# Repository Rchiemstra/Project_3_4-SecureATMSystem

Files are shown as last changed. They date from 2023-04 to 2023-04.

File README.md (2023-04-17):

# Project_3_4-SecureATMSystem

Dit project betreft het opzetten van een bankomgeving met pinautomaten, geldautomaten en beveiliging. Studenten richten in groepen banken op en verzorgen interbancaire communicatie.

## Beschrijving

Dit project betreft de ontwikkeling van een complete bankomgeving, waarbij studenten in groepen een eigen bank zullen oprichten binnen een land en de complexiteit van samenwerking tussen verschillende groepsbanken zullen simuleren. De architectuur van het systeem zal worden ontworpen met aandacht voor kwaliteitsattributen, waaronder security, betrouwbaarheid en robuustheid.

Het project omvat de ontwikkeling van software- en hardwarecomponenten die betrokken zijn bij het pinnen van geld, inclusief geldautomaten en gelddispensers. Daarnaast zullen de studenten zich bezighouden met de communicatie tussen banken, zodat het voor de eindgebruiker mogelijk wordt om bij een andere groepsbank te pinnen op basis van eigen gegevens (pinpas en saldo).

Elke groep zal een land vertegenwoordigen en een eigen bank oprichten. Het project omvat het ontwerpen en ontwikkelen van software voor het beheer van rekeningen, pinautomaten en geldautomaten, evenals het ontwerpen en implementeren van beveiligingsmaatregelen om de privacy en veiligheid van gebruikersgegevens te waarborgen.

Dit project biedt studenten de kans om in een realistische omgeving te werken aan een complex systeem en belangrijke technische vaardigheden te ontwikkelen, zoals systeemarchitectuur, software- en hardwareontwerp en beveiligingsimplementatie.

### Team

| Naam | LinkedIn |
| --- | --- |
| Ruben Hiemstra | [LinkedIn](https://www.linkedin.com/in/ruben-hiemstra-84b9b6127/) |
| Keanu van der Linden | [LinkedIn](https://github.com/KeanuLin) |
| TBA | [LinkedIn] |
| TBA | [LinkedIn] |
| TBA | [LinkedIn] |

### Bestanden / Files

#### doc
Deze map bevat documentatie over het project. Er is een submap genaamd "Fusion360" die 3D-modellen bevat van verschillende componenten in het project, zoals geldautomaten en pinautomaten. Er is ook een PDF-bestand genaamd "pinautomaat v6 v16.pdf" dat een tekening bevat van een pinautomaat. Verder bevat deze map een submap genaamd "img" met afbeeldingen die worden gebruikt in de documentatie van het project.

#### img 
Deze map bevat afbeeldingen die in het project worden gebruikt. Er zijn drie submappen:

- eurobiljetten: Deze submap bevat afbeeldingen van verschillende eurobiljetten, inclusief "10_euro.jpeg", "20_euro.jpeg" en "50_euro.jpeg".

- geldautomaat_spiraal_unittest: Deze submap bevat afbeeldingen die zijn gebruikt bij het testen van de code voor de geldautomaat.

- UI_Ruben_Hiemstra: Deze submap bevat afbeeldingen van de gebruikersinterface van het bankgedeelte van het project, gemaakt door Ruben Hiemstra. Er zijn 12 PNG-bestanden genaamd "1.PNG" tot en met "12.PNG" die screenshots bevatten van verschillende delen van de UI.
README.md: Dit bestand bevat de beschrijving van het project en de inhoud van deze README.

#### src
Deze map bevat alle broncode voor het project, georganiseerd in verschillende submappen.

- Arduino: Deze map bevat de broncode voor de Arduino-microcontroller die wordt gebruikt in het project. Er zijn verschillende submappen binnen "Arduino" die code bevatten voor specifieke componenten en functies, waaronder tests voor verschillende componenten zoals RFID-kaarten en keypads, code voor het printen van bonnen en code voor de master- en node-nodes.

- UI: Deze map bevat de broncode voor de gebruikersinterface van het bankgedeelte van het project, geschreven in Java. Er is een submap genaamd ".vscode" met instellingen voor de Visual Studio Code-editor. De "bank" submap bevat broncode voor het beheer van rekeningen, pinautomaten en geldautomaten, evenals tests en afbeeldingen. De pom.xml-file is een Maven-bestand dat nodig is om de Java-code in dit project te compileren en uit te voeren.

### Media

## Rubben Hiemstra

#### Ontwerp pinautomaat

<a href="https://youtu.be/MVlD1MDzszY" target="_blank"   rel="noopener"  >
    
</a>

#### Test pinautomaat

<a href="https://youtu.be/q1xSIUnEXdo" target="_blank"   rel="noopener"  >
    
</a>

## Groepsgedeelte

#### Ontwerp geldlade

<a href="https://youtu.be/ZYODidJn9q8" target="_blank"   rel="noopener"  >
    
</a>

#### Ontwerp geldlades

<a href="https://youtu.be/2BWyQDWWHVI" target="_blank"   rel="noopener"  >
    
</a>

#### Pinpas blokkeren voor alle bij alle pinautomaten

<a href="https://youtu.be/CWAH8InKsuk" target="_blank"   rel="noopener"  >
    
</a>

#### Meerdere pinautomaten tegelijk

<a href="https://youtu.be/7Nd1Y9njzbA" target="_blank"   rel="noopener"  >
    
</a>

### unittest

Geldautomaat spiraal - Unit test

Voor ons bankproject moeten we geld kunnen afgeven nadat er is gepind. Daarom moeten we een systeem bedenken dat veilig is en geen geld verliest. We hebben besloten om een spiraal te gebruiken waar het geld uit kan vallen. Om zo'n spiraal te maken, hebben we verschillende methoden uitgeprobeerd: het vervormen van staaldraad, 3D-printen en online zoeken. Hieronder beschrijven we de stappen die we hebben genomen tot aan onze beslissing.

<table >
  <tbody>
    <tr>
      <th>Poging 1</th>
    </tr>
    <tr>
      <td>De grijze/De witte</td>
    </tr>
    <tr>
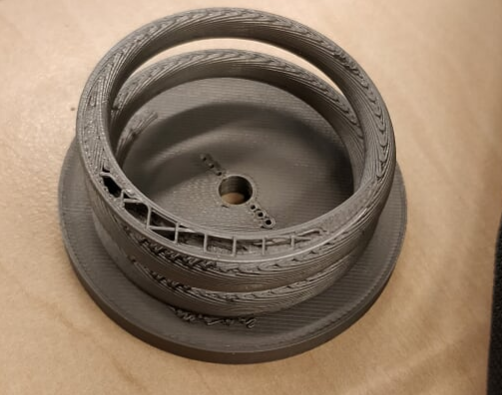
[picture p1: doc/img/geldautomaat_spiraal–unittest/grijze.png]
      <td>
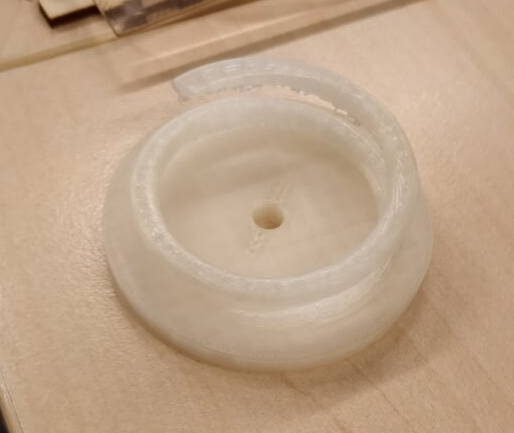
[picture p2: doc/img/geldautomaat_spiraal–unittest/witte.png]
      </td>
    </tr>
    <tr>
      <td>De grijze spiraal is hetzelfde als de witte, maar we hebben ondersteuning gebruikt tijdens het printen. Hierdoor ziet het er beter uit en zijn de cirkels gladder, waardoor het papier niet vast komt te zitten. Helaas hebben we te veel ruimte tussen de cirkels weggehaald, waardoor de ruimte te krap was en de cirkels te zwak waren. Deze poging voldeed daarom niet aan onze eisen.</td>
    </tr>
    <tr>
      <td>Dit is een klein stukje van een 3D-geprinte spiraal. We hebben geen ondersteuning gebruikt tijdens het printen, waardoor er gesmolten plastic aan de onderkant hangt dat het papier kan vasthouden. Bovendien was de ruimte tussen de cirkels waar het papier doorheen moet te groot, waardoor we maar weinig papier konden vasthouden. Om meer papier op te slaan, moeten we de diameter of de dikte van de cirkels verminderen om meer ruimte te creëren.</td>
    </tr>
  </tbody>
</table>

<table>
  <tbody>
    <tr>
      <th>Poging 2</th>
    </tr>
    <tr>
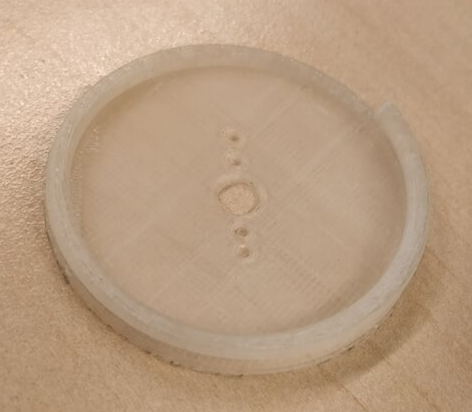
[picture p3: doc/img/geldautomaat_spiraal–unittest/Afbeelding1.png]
      <td>
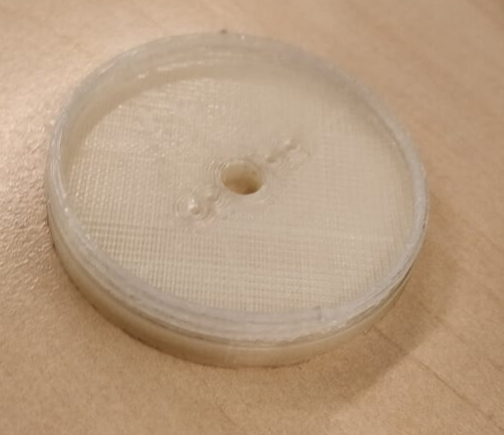
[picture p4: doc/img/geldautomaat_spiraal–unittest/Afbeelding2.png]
      </td>
    </tr>
    <tr>
      <td><p>Bij deze spiraal hebben we meer ruimte voor het papier gemaakt door de afstand tussen de cirkels en de diameter van de cirkels te verminderen. Helaas hebben we te veel afstand weggehaald, waardoor de ruimte te krap was en de cirkels te zwak waren. Deze poging voldeed daarom ook niet aan onze eisen.</p></td>
    </tr>
  </tbody>
</table>

<table>
  <tbody>
    <tr>
      <th>Poging 3</th>
    </tr>
    <tr>
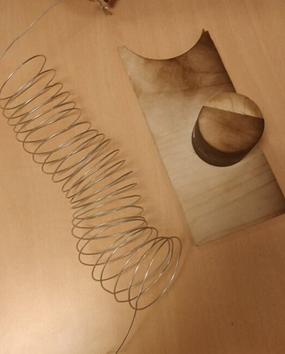
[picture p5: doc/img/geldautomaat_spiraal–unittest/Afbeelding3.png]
      <td></td>
    </tr>
    <tr>
      <td><p>Bij deze poging hebben we geprobeerd staaldraad te gebruiken, omdat dit stevig is en vervormd kan worden. We hebben een stuk hout gebruikt om de draad omheen te draaien en het daarna een tijdje laten zitten om te zorgen dat het goed bleef zitten. Helaas bleek na het verwijderen van de draad dat deze zeer asymmetrisch was en niet bruikbaar was. We zijn daarom teruggegaan naar de 3D-printer.</p></td>
    </tr>
  </tbody>
</table>

<table>
  <tbody>
    <tr>
      <th>Poging 4</th>
    </tr>
    <tr>
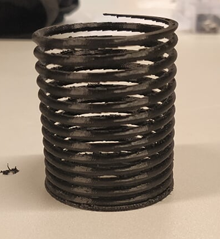
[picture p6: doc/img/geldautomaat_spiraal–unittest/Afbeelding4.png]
      <td> </tr>
    <tr>
      <td><p>Bij deze 3D-print hebben we ondersteuning gebruikt en hebben we de afmetingen op alle mogelijke manieren geoptimaliseerd (dikte, afstand tussen de cirkels en de voet van de print). Dit zou de definitieve versie worden, maar helaas is de 3D-printer uitgevallen en konden we niet verder gaan. We hebben daarom maar de helft van de spiraal kunnen printen. Desondanks zijn we zeer tevreden met het resultaat en zullen we dit gebruiken in onze geldautomaat.</p></td>
    </tr>
  </tbody>
</table>

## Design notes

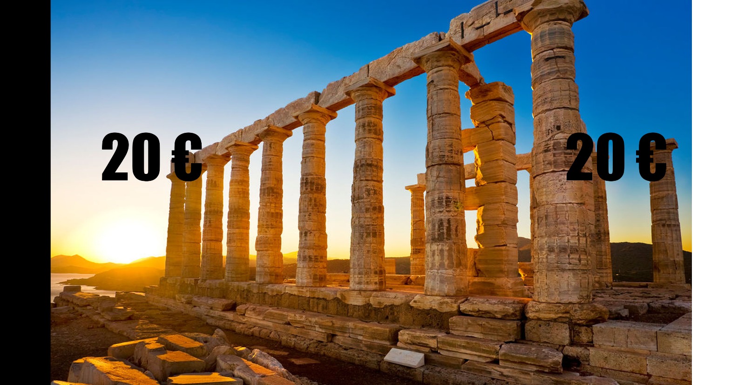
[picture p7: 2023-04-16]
doc/img/eurobiljetten/20_euro.jpeg

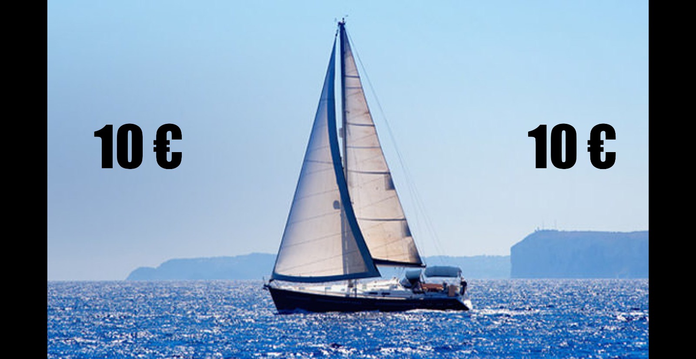
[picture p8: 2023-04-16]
doc/img/eurobiljetten/10_euro.jpeg

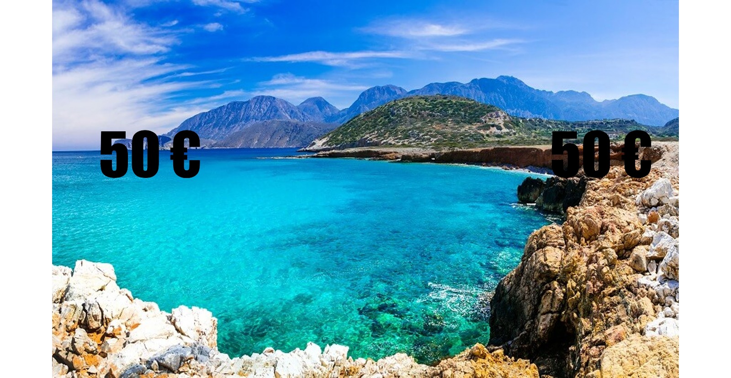
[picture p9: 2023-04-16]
doc/img/eurobiljetten/50_euro.jpeg

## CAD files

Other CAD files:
doc/Fusion360/geldautomaat v12.f3d
doc/Fusion360/geldautomaat v2.f3d
doc/Fusion360/pinautomaat v6 v16.f3d
doc/Fusion360/spiraal v25.f3d

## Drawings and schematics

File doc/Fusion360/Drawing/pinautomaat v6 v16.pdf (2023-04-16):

16.01 6

16

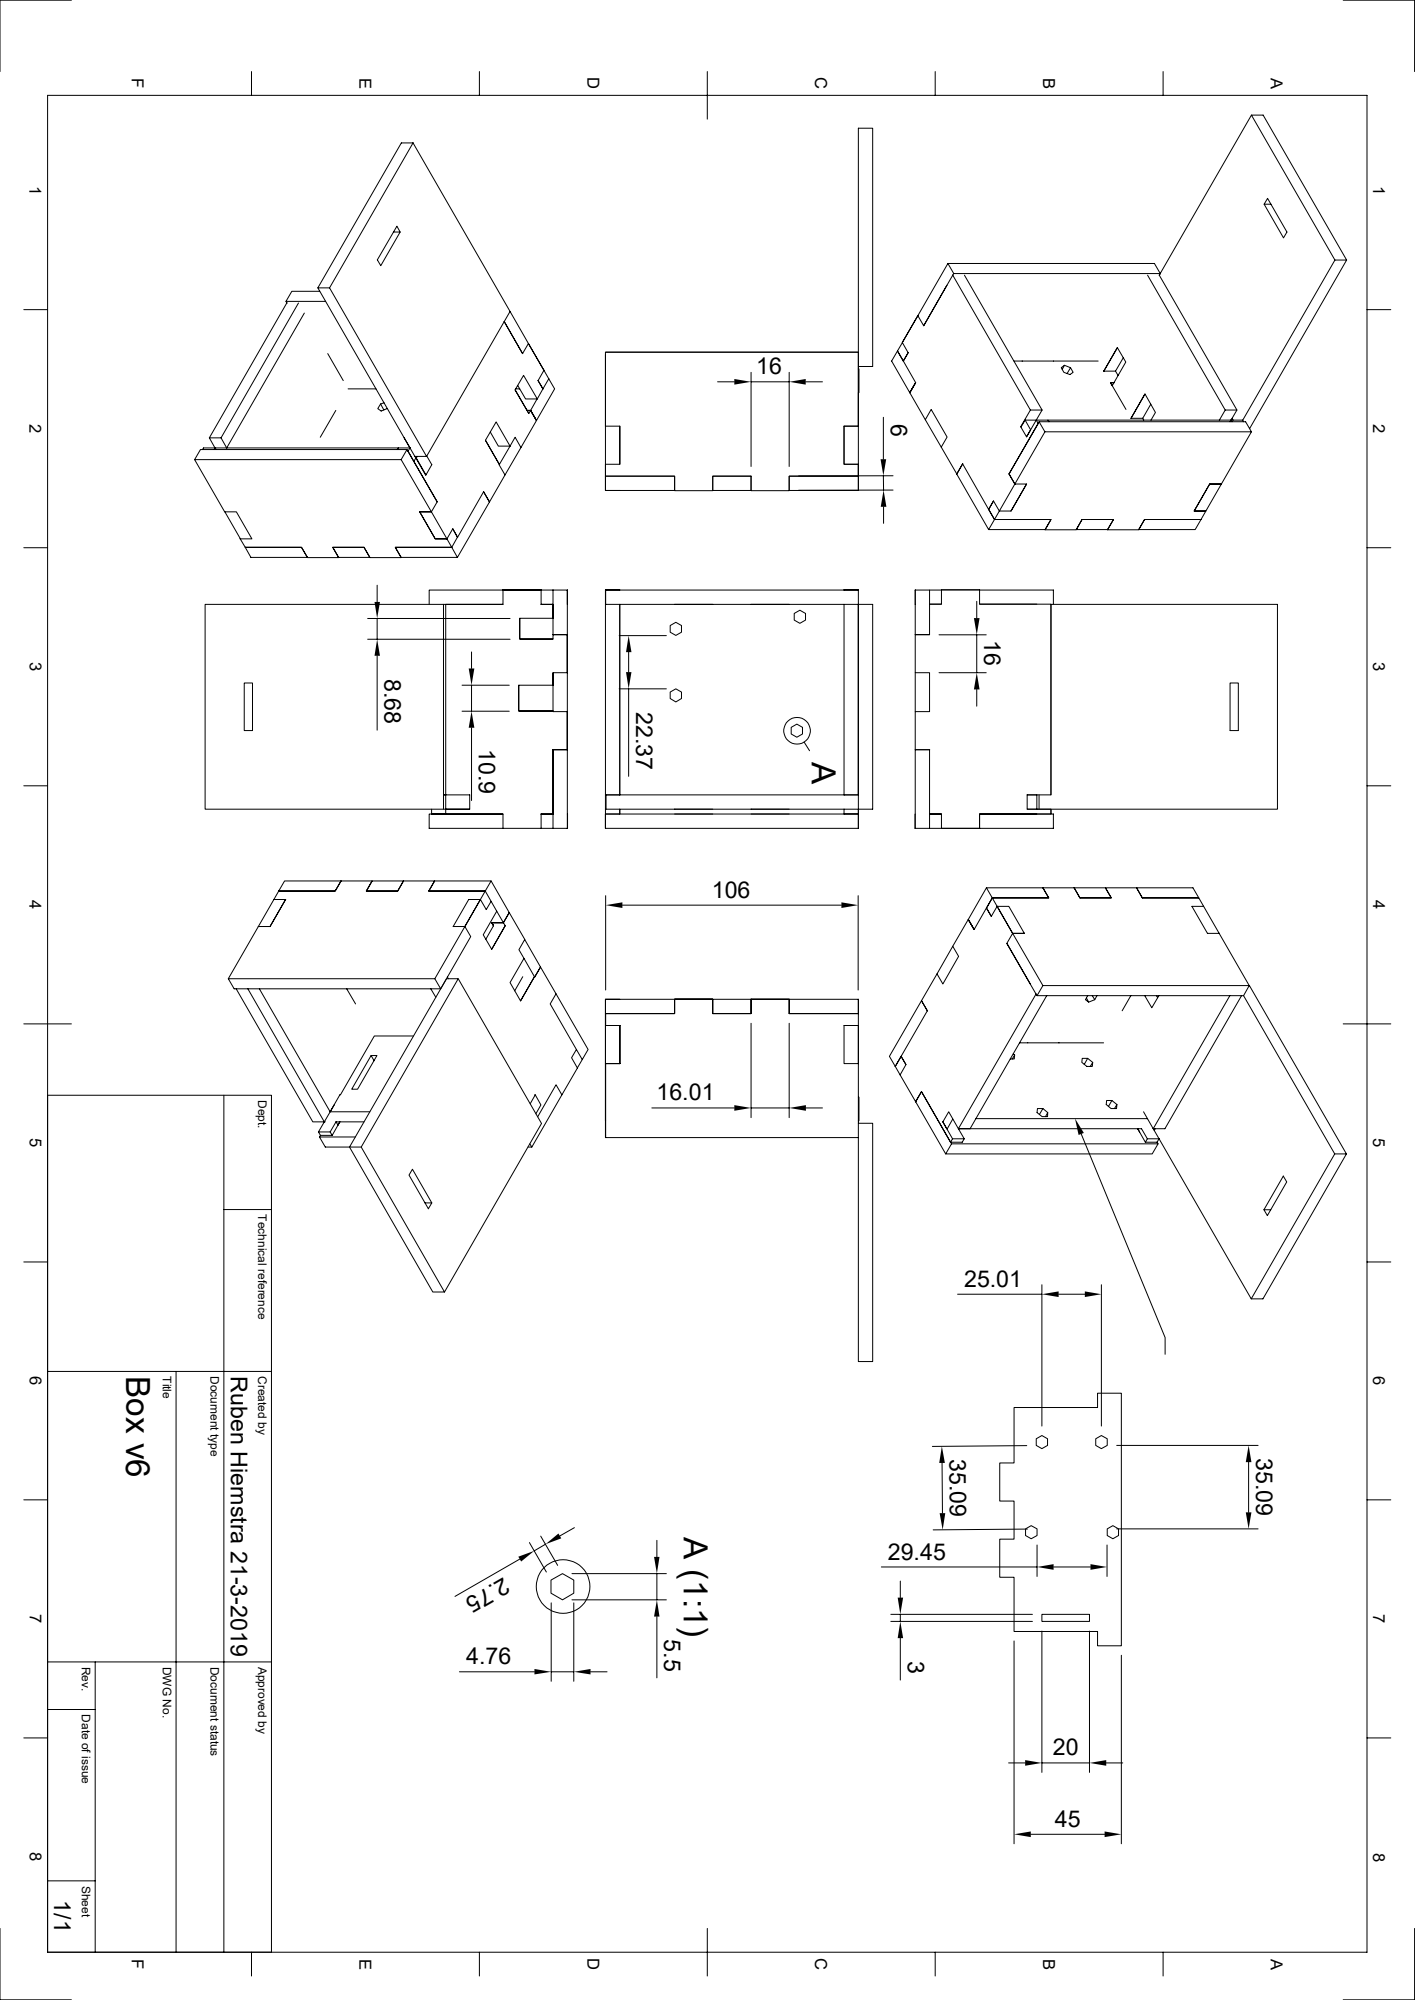
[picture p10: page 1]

1 A 2 3 4 5 6 7 8 1 2 3 4 5 6 7 8 FEDCB FEDCBA Dept. Technical reference Created by Approved by Title DWG No. Document type Document status Rev. Date of issue Sheet 21-3-2019 1/1 Box v6 Ruben Hiemstra

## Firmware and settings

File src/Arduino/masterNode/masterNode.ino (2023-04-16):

#include <SoftwareSerial.h>



////////////////////////WERKENDE I2C MASTER ALS TEST////////////////


// Wire Master Reader
// by Nicholas Zambetti <http://www.zambetti.com>

// Demonstrates use of the Wire library
// Reads data from an I2C/TWI slave device
// Refer to the "Wire Slave Sender" example for use with this

// Created 29 March 2006

// This example code is in the public domain.

#include <Wire.h>
// Include the Servo library 
#include <Servo.h> 
#include "Adafruit_Thermal.h"
#include "adalogo.h"
#include "adaqrcode.h"
#include "SoftwareSerial.h"

char c1;
char c2;
char c3;
char c4;
char c5;
char c6;
char c7;
char c8;
char c9;
char c10;
char c11;
char c12;
char c13;
char c14;

String rekeningstring;

int totaal;
int e;
char metbon;

char aantal10;
int aantal10int;
char aantal20;
int aantal20int;
char aantal50;
int aantal50int;

// Declare the Servo pin 
int ServoPin1 = 11; 
// Create a servo object 
Servo Servo1; 
// Declare the Servo pin 
int ServoPin2 = 10; 
// Create a servo object 
Servo Servo2; 
// Declare the Servo pin 
int ServoPin3 = 3; 
// Create a servo object 
Servo Servo3; 

#define TX_PIN 6 // Arduino transmit  YELLOW WIRE  labeled RX on printer
#define RX_PIN 5 // Arduino receive   GREEN WIRE   labeled TX on printer

SoftwareSerial mySerial(RX_PIN, TX_PIN); // Declare SoftwareSerial obj first
Adafruit_Thermal printer(&mySerial);     // Pass addr to printer constructor

void setup() {
  Wire.begin();        // join i2c bus (address optional for master)
  Serial.begin(9600);  // start serial for output
  // We need to attach the servo to the used pin number 
  Servo1.attach(ServoPin1); 
  Servo2.attach(ServoPin2); 
  Servo3.attach(ServoPin3); 

}

void loop() {
    for (int i = 8; i <= 11; i++) {

OGloop(i);
if (rekeningstring != "" || rekeningstring != NULL) {
  totaal = 0;
  int telling10 = 0;
  while (aantal10int > telling10) {
    motor1();
    Serial.println("draai 1 keer voor motor 1");
    delay(1000);
    totaal = totaal + 10;
    telling10++;
  }
  int telling20 = 0;
  while (aantal20int > telling20) {
    motor2();
        Serial.println("draai 1 keer voor motor 2");

    delay(1000);
    totaal = totaal + 20;
    telling20++;
  }
  int telling50 = 0;
  while (aantal50int > telling50)
  {
    motor3();
        Serial.println("draai 1 keer voor motor 3");

    delay(1000);
    totaal = totaal + 50;
    telling50++;
  }
  if (metbon == 'j') {
    boncode();
    Serial.println("bon succesvol uitgeprint");
    metbon = 'n';
  }
}
Serial.println(totaal);
delay(1000);
    }
}

void OGloop(int i) {
  rekeningstring = "";
  //for (int i = 8; i <= 11; i++) {
    //int re_i = i + 2;
    Wire.requestFrom(i, 18);    // request 6 bytes from slave device #8
 // }

  while (Wire.available()) { // slave may send less than requested
    c1 = Wire.read(); // receive a byte as character
    rekeningstring += c1;
    c2 = Wire.read(); // receive a byte as character
    rekeningstring += c2;
    c3 = Wire.read(); // receive a byte as character
    rekeningstring += c3;
    c4 = Wire.read(); // receive a byte as character
    rekeningstring += c4;
    c5 = Wire.read(); // receive a byte as character
    rekeningstring += c5;
    c6 = Wire.read(); // receive a byte as character
    rekeningstring += c6;
    c7 = Wire.read(); // receive a byte as character
    rekeningstring += c7;
    c8 = Wire.read(); // receive a byte as character
    rekeningstring += c8;
    c9 = Wire.read(); // receive a byte as character
    rekeningstring += c9;
    c10 = Wire.read(); // receive a byte as character
    rekeningstring += c10;
    c11 = Wire.read(); // receive a byte as character
    rekeningstring += c11;
    c12 = Wire.read(); // receive a byte as character
    rekeningstring += c12;
    c13 = Wire.read(); // receive a byte as character
    rekeningstring += c13;
    c14 = Wire.read(); // receive a byte as character
    rekeningstring += c14;

    //totaal = Wire.read();
    //e = Wire.read();

    aantal10 = Wire.read();
    aantal20 = Wire.read();
    aantal50 = Wire.read();

    metbon = Wire.read();

    String converter = "";
    converter += aantal10;
    aantal10int = converter.toInt();
    converter = "";
    converter += aantal20;
    aantal20int = converter.toInt();
    converter = "";
    converter += aantal50;
    aantal50int = converter.toInt();
    
    Serial.println(rekeningstring);         // print the character
    
    //delay(1000);
    Serial.println(totaal);         // print the character
    //delay(1000);

    Serial.println(e);         // print the character
    //delay(1000);

    Serial.println(aantal10);
    //delay(250);

    Serial.println(aantal20);
    //delay(250);

    Serial.println(aantal50);
    //delay(250);

    Serial.println(metbon);
    //delay(1000);

  //}
  }

  delay(500);
}

void motor1() {
   Servo1.write(110);  
   delay(4200); 
   Servo1.write(90);
}

void motor2() {
   // Make servo go to 0 degrees 
   Servo2.write(110); 
   delay(4200);
   // Make servo go to 90 degrees 
   Servo2.write(90); 
}

void motor3() {
   // Make servo go to 0 degrees 
   Servo3.write(110); 
   delay(4200);
   // Make servo go to 90 degrees 
   Servo3.write(90); 
}

void boncode() {
  // This line is for compatibility with the Adafruit IotP project pack,
  // which uses pin 7 as a spare grounding point.  You only need this if
  // wired up the same way (w/3-pin header into pins 5/6/7):
  pinMode(7, OUTPUT);
  digitalWrite(7, LOW);

  // NOTE: SOME PRINTERS NEED 9600 BAUD instead of 19200, check test page.
  mySerial.begin(9600);  // Initialize SoftwareSerial
  //Serial1.begin(19200); // Use this instead if using hardware serial
  printer.begin();        // Init printer (same regardless of serial type)

  // The following calls are in setup(), but don't *need* to be.  Use them
  // anywhere!  They're just here so they run one time and are not printed
  // over and over (which would happen if they were in loop() instead).
  // Some functions will feed a line when called, this is normal.

  // Test inverse on & off
  printer.doubleHeightOn();
  printer.setLineHeight(50);
  printer.boldOn();
  printer.justify('C');
  printer.setSize('L');
  printer.println(F("F.A.I.L."));
  
  printer.boldOff();
  printer.doubleHeightOff();
  printer.setSize('S');
  printer.println(F("2019"));
  
  printer.setLineHeight(0);
  printer.justify('L');
  printer.setSize('S');
  printer.println(F(""));
  printer.println(rekeningstring);
//  printer.print(F(str(c2)));
//  printer.print(F(str(c3)));
//  printer.print(F(str(c4)));
//  printer.print(F(str(c5)));
//  printer.print(F(str(c6)));
//  printer.print(F(str(c7)));
//  printer.print(F(str(c8)));
//  printer.print(F(str(c9)));
//  printer.print(F(str(c10)));
//  printer.print(F(str(c11)));
//  printer.print(F(str(c12)));
//  printer.print(F(str(c13)));
//  printer.print(F(str(c14)));

  printer.println("Het totaal gepinde bedrag: ");
  printer.print(totaal);
  printer.print(" Euro");

  printer.println(F(""));
  printer.println(F(""));
  printer.justify('C');
  printer.setSize("M");
  printer.println(F("BEDANKT VOOR HET PINNEN"));
  printer.println(F(""));
  printer.println(F(""));
  printer.println(F(""));
  
  printer.feed(2);

  printer.sleep();      // Tell printer to sleep
  delay(3000L);         // Sleep for 3 seconds
  printer.wake();       // MUST wake() before printing again, even if reset
  printer.setDefault(); // Restore printer to defaults

}

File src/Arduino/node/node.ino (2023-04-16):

#include <SPI.h>
#include <MFRC522.h>
#include <Keypad.h>
#include <Wire.h>
#define SS_PIN 10
#define RST_PIN 9
MFRC522 mfrc522(SS_PIN, RST_PIN);   // Create MFRC522 instance.


// Change te block where the bank number is stored.
int block = 1;

byte readBackBlock[14];
MFRC522::MIFARE_Key key;
String a;
const byte ROWS = 4; //four rows
const byte COLS = 4; //three
char rekeningnummer[19] = "";
int bedrag = 70;
int totaal = 200;
int aantal10 = 0;
int dddd = 1;
int getal;
int m = 0;
int aantal20 = 0;
int aantal50 = 0;
boolean klaarOmTeGaan = false;
String Text = "";
//define the symbols
char stdKeys[ROWS][COLS] = {
  { '1' , '2' , '3' , 'A' },
  { '4' , '5' , '6' , 'B' },
  { '7', '8', '9', 'C' },
  { '*' , '0' , '#' , 'D'}
};
byte rowPins[ROWS] = {A0, 2, 3, 4}; //connect to the row pinouts of the keypad
byte colPins[COLS] = {5, 6, 7, 8}; //connect to the column pinouts of the keypad
int PinCode = 0;
byte digitCount = 0;

//initialize an instance of class NewKeypad
Keypad customKeypad = Keypad( makeKeymap(stdKeys), rowPins, colPins, ROWS, COLS);




void setup()
{
  Serial.begin(9600);   // Initiate a serial communication
  SPI.begin();      // Initiate  SPI bus
  mfrc522.PCD_Init();   // Initiate MFRC522
  Wire.begin(8);                // join i2c bus with address #8
  Wire.onRequest(requestEvent); // register event

}
void loop() {
  if (Serial.available()) {
    while (Serial.available()) {
      a = Serial.readString(); // read the incoming data as string
       Serial.println("arduino zegt"+a);
      if (a != "" || a != NULL) {
        a.toCharArray(rekeningnummer, 19);
      }
    }
  }

  if (char Key = customKeypad.getKey()) {
    Serial.print("XXXXXXXXXXXXXX-");
    Serial.println(Key);
  }
  /*
  if ( ! mfrc522.PICC_IsNewCardPresent())
  {
    return;
  }
  // Select one of the cards
  if ( ! mfrc522.PICC_ReadCardSerial())
  {
    return;
  }
  //Show UID on serial monitor
  String content = "";
  byte letter;
  for (byte i = 0; i < mfrc522.uid.size; i++) {
    Serial.print(mfrc522.uid.uidByte[i] < 0x10 ? " 0" : " ");
    Serial.print(mfrc522.uid.uidByte[i], HEX);
    content.concat(String(mfrc522.uid.uidByte[i] < 0x10 ? " 0" : " "));
    content.concat(String(mfrc522.uid.uidByte[i], HEX));

  }
  content.toUpperCase();*/
  RFIDcode();

}

void requestEvent() {
  int i = 0;
  while (i < 18) {
    Wire.write(rekeningnummer[i]); // respond with message of 6 bytes
    rekeningnummer[i] = char(0);
    i++;
  }
}

void RFIDcode() {
  // Look for new cards
  if ( ! mfrc522.PICC_IsNewCardPresent())
  {
    return;
  }
  // Select one of the cards
  if ( ! mfrc522.PICC_ReadCardSerial())
  {
    return;
  }

      // Set authentication key
    for (byte index = 0; index < 6; index++) {
        key.keyByte[index] = 0xFF;
    }
      readBlock(block, readBackBlock);
          String content = "";
    for(int index = 0; index < sizeof(readBackBlock); index++){
        content += char(readBackBlock[index]);
    }
    Serial.print(content);
    Serial.println("-X");
    // End authentication
    mfrc522.PICC_HaltA();
    mfrc522.PCD_StopCrypto1();
}

void readBlock(int blockNumber, byte arrayAddress[]){
    authenticateBlockAction(block);

    byte buffersize = 18;

    byte status = mfrc522.MIFARE_Read(blockNumber, arrayAddress, &buffersize);\
    if (status != MFRC522::STATUS_OK) {
        //Serial.println("Read failed");
            mfrc522.PICC_HaltA();
    mfrc522.PCD_StopCrypto1();
        loop();
        //return;
    }

    //Serial.println("Block was read");
}

void authenticateBlockAction(int blockNumber){
    int largestModulo4Number = blockNumber / 4 * 4;
    int trailerBlock = largestModulo4Number + 3;

    byte status = mfrc522.PCD_Authenticate(MFRC522::PICC_CMD_MF_AUTH_KEY_A, trailerBlock, &key, &(mfrc522.uid));
    if (status != MFRC522::STATUS_OK) {
        Serial.println("Authentication failed");
        return;
    }
}
